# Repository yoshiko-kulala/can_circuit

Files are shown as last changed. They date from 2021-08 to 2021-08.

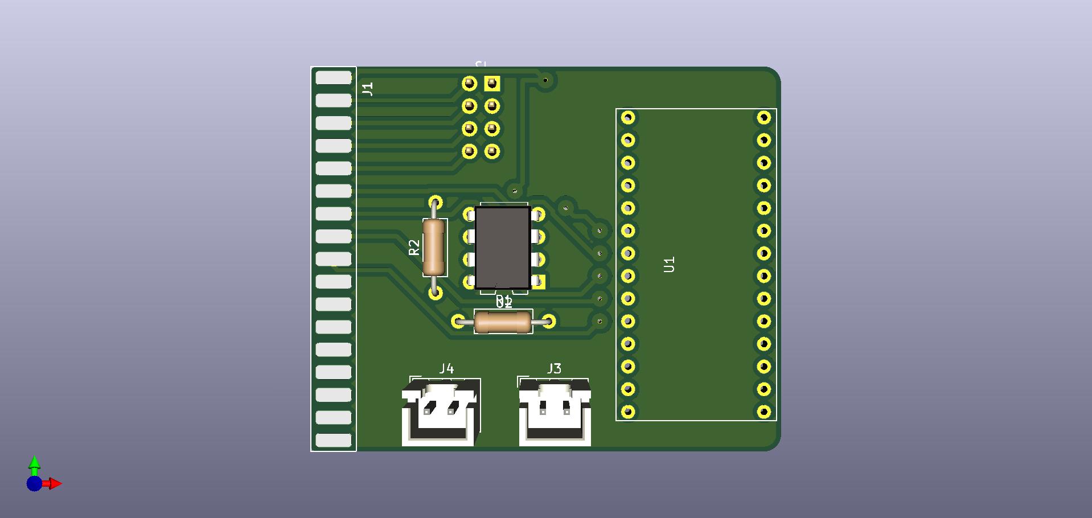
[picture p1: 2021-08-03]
RIOboard/circuit/RIOboard/RIOboard.jpg

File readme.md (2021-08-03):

# ロボット用can通信基板
このリポジトリはcan通信を用いてロボットのセンサやアクチュエータと通信・制御するための基板が置いてあります。  

各基板ごとに回路図、kicadプロジェクトデータ、サンプルプログラムが含まれます。  
自由に複製してロボットに用いることが出来ます。

can通信のid、内容については下記の各項目で示します。
通信速度は1Mbpsです。

## bumperboard
デジタルのスイッチとADCの信号を読み取ることが出来ます。  
デジタル信号が4つ、ADCは8bitが8チャネルあります。  
メインMCUにはteensy3.2を使用、can通信の通信内容は以下の通りです。  
### 0x001
| buf[1] | 中身 | 備考 |
| --- | --- | --- |
| buf[0] | デジタル信号 | 4つの入力の論理和 |
### 0x003
| buf[8] | 中身 | 備考 |
| --- | --- | --- |
| buf[0] | A0 | 0~255 |
| buf[1] | A1 |  |
| buf[2] | A2 |  |
| buf[3] | A3 |  |
| buf[4] | A4 |  |
| buf[5] | A5 |  |
| buf[6] | A6 |  |
| buf[7] | A7 |  |

## encoderboard  
インクリメントエンコーダを読み取り、回転速度と積分量を返します。  
エンコーダは最大3つまで搭載できます。
MCUにはstm32f303k8を使用し、ハードウェアデコーダを用いてエンコーダの読み取りを行っています。
can通信の内容は以下の通りです。
### 0x301
| buf[8] | 中身 | 備考 |
| --- | --- | --- |
| buf[0] | エンコーダ0のカウント下8bit | 速度は10bit |
| buf[1] | エンコーダ0のカウント上2bitとエンコーダ1のカウント下6bit |  |
| buf[2] | エンコーダ1のカウント下4bitとエンコーダ2のカウント下4bit |  |
| buf[3] | エンコーダ2のカウント下6bit |  |
| buf[4] | 未使用 |  |
| buf[5] | 未使用 |  |
| buf[6] | 未使用 |  |
| buf[7] | 未使用 |  |
### 0x302
| buf[8] | 中身 | 備考 |
| --- | --- | --- |
| buf[0] | エンコーダ0のカウント下8bit | 上下合成して0~65536 |
| buf[1] | エンコーダ0のカウント上8bit |  |
| buf[2] | エンコーダ1のカウント下8bit | 上下合成して0~65536 |
| buf[3] | エンコーダ1のカウント上8bit |  |
| buf[4] | エンコーダ2のカウント下8bit | 上下合成して0~65536 |
| buf[5] | エンコーダ2のカウント上8bit |  |
| buf[6] | 未使用 |  |
| buf[7] | 未使用 |  |

## purin_main_board  
ブザーやジャイロ、コントローラ用の通信口を持った基板  
モータドライバとも接続可能で足回りの駆動系と通信することが出来る  
DJIのDR16と接続することでコントローラとの通信も可能
この基板についてはデバッグ用のcan受信プログラムが書かれている。使途に合わせて自由な内容を受信し、それに合わせてブザーを鳴らしたりモータを動かすことが可能である。

## RIOboard  
myRIOと接続し、can通信とmyRIOをつなげる基板  
myRIOとはGPIO4つとuartで接続されている。
また、myRIOからスレーブコントローラ用へのUSBコネクタも内包している。
この基板もmyRIOからの信号に合わせて自由に通信内容を決めることが出来る。

## stepperboard  
ステッピングモータを駆動させるための基板  
L6470とSPI通信を行い、最大3つのステッピングモータを駆動可能  
電源供給用のコネクタやリミットスイッチの入力コネクタも実装済  
サーボを1つまで接続し動作させることが出来る  
can通信の内容は以下の通り  
### 0x2F1
| buf[8] | 中身 | 備考 |
| --- | --- | --- |
| buf[0] | 現在のx軸(左右)の下8bit | x上限は4374  センターは2768 |
| buf[1] | 現在のx軸(左右)の上8bit | 下限が左 |
| buf[2] | 現在のy軸(上下)の下8bit | y上限は4050 |
| buf[3] | 現在のy軸(上下)の上8bit | 下限が上 |
| buf[4] | 現在のz軸(前後)の下8bit | z上限は31500 |
| buf[5] | 現在のz軸(前後)の上8bit | 下限が後 |
| buf[6] | ハンド | 1で閉じてる、0で開いてる |
| buf[7] | 未使用 |  |
### 0x2F2
| buf[8] | 中身 | 備考 |
| --- | --- | --- |
| buf[0] | 目標のx軸(左右)の下8bit | x上限は4374  センターは2768 |
| buf[1] | 目標のx軸(左右)の上8bit | 下限が左 |
| buf[2] | 目標のy軸(上下)の下8bit | y上限は4050 |
| buf[3] | 目標のy軸(上下)の上8bit | 下限が上 |
| buf[4] | 目標のz軸(前後)の下8bit | z上限は31500 |
| buf[5] | 目標のz軸(前後)の上8bit | 下限が後 |
| buf[6] | ホーム復帰 | 1でホーム復帰 |
| buf[7] | 未使用 |  |
### 0x2F3
msg.len=1
| buf[1] | 中身 | 備考 |
| --- | --- | --- |
| buf[0] | ハンド開閉 | 0が閉じている、1が開いてる |

## UIboard  
デジタルの信号入力が4つ、ws2812bというマイコン内蔵RGBLEDの制御信号を出すことが出来る  
非常停止スイッチが取り付けられることを想定してcanのidは0となっており最優先で信号が送られる。  
通信内容は以下の通り。  
### 0x000
| buf[8] | 中身 | 備考 |
| --- | --- | --- |
| buf[0] | 状態 | 現在のライトの色 |
| buf[1] | 非常停止スイッチ | 押下状態で0 |
| buf[2] | リセットスイッチ | 押下状態で0 |
| buf[3] | 起動スイッチ | 押下状態で0 |
| buf[4] | 空き | 押下状態で0 |
| buf[5] | 未使用 |  |
| buf[6] | 未使用 |  |
| buf[7] | 未使用 |  |

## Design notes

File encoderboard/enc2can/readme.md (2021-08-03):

# enc2can

エンコーダを読んでcanで送る基板とプログラム  

送信側はnucleo f303k8  
受信側はteensy3.2

トランシーバーはmcp2551  

canidは0x301(切り替えるdipを基板につけ忘れたので...)

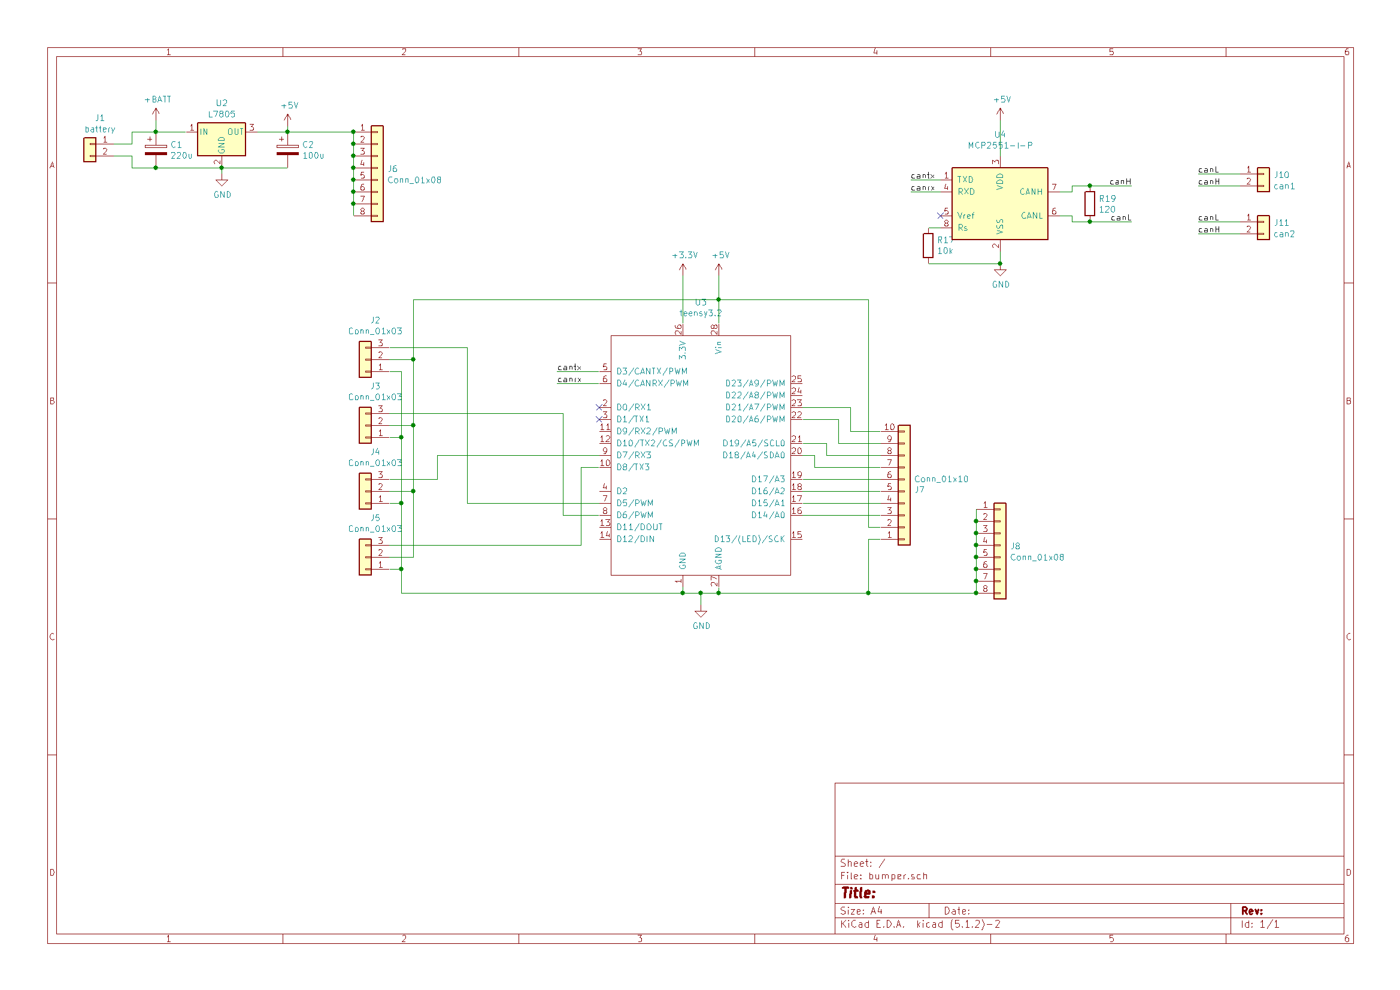
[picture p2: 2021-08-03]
bumperboard/circuit/circuit.png

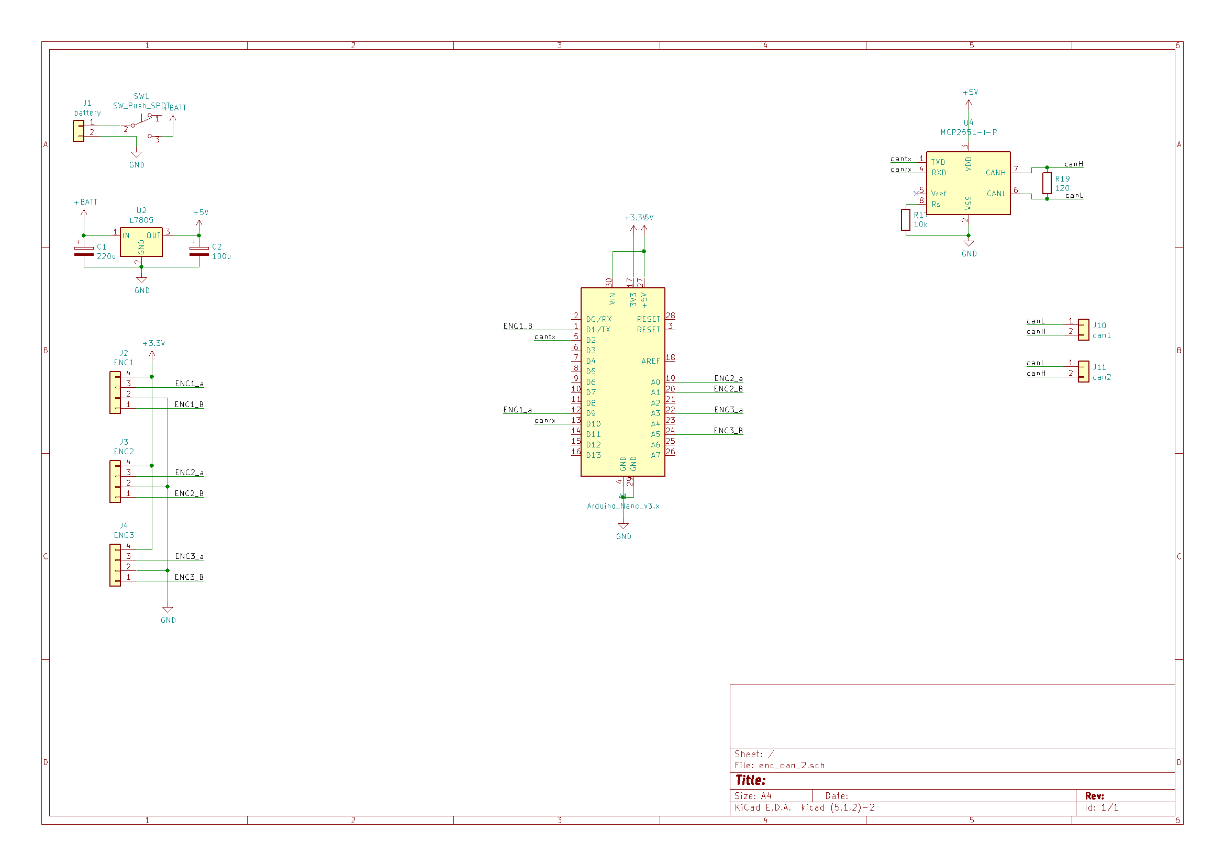
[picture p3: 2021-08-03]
encoderboard/circuit/circuit.png

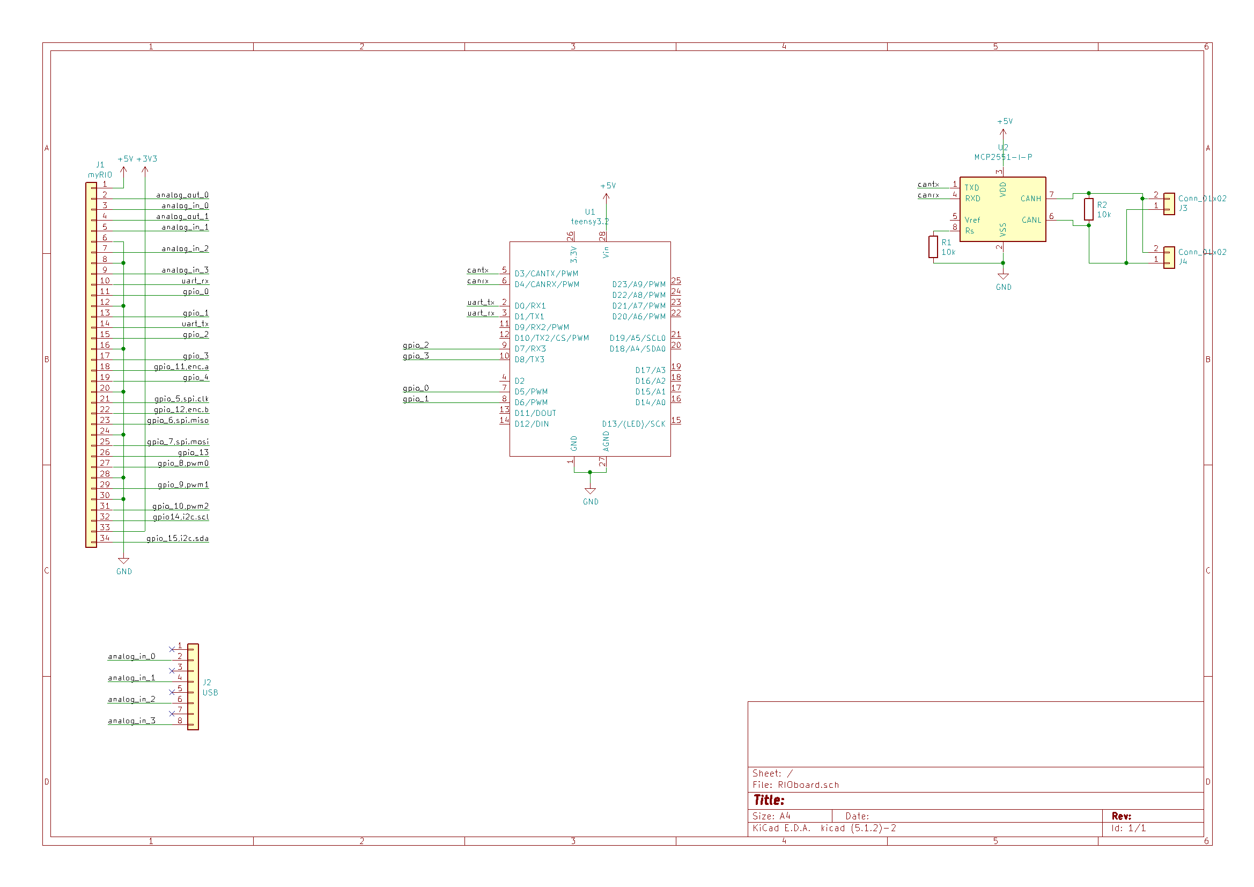
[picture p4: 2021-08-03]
RIOboard/circuit/circuit.png

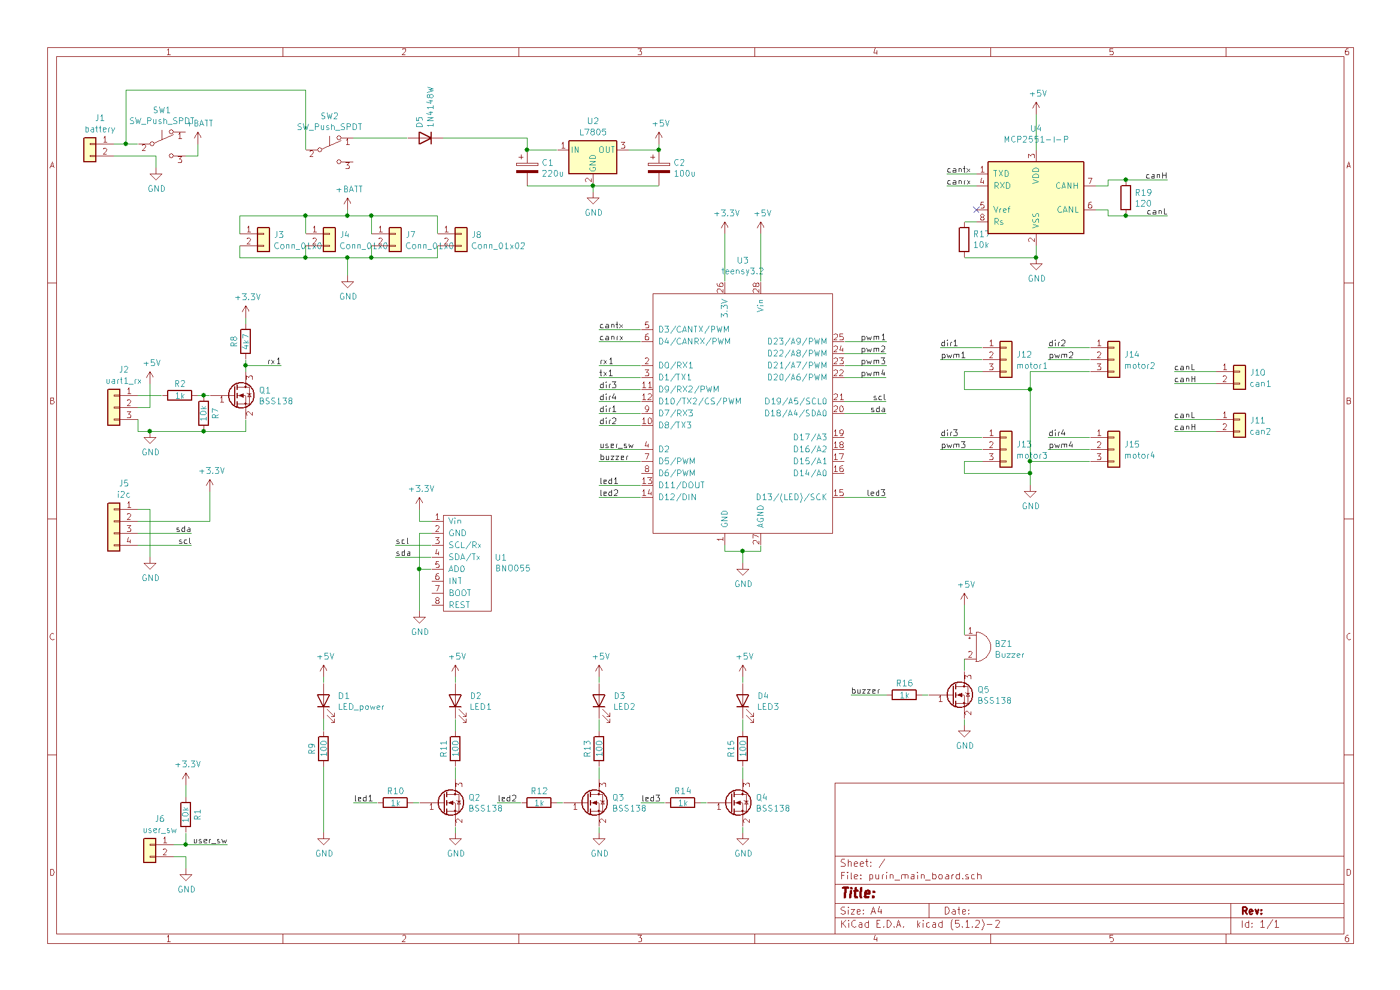
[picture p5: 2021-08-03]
purin_main_board/circuit/circuit.png

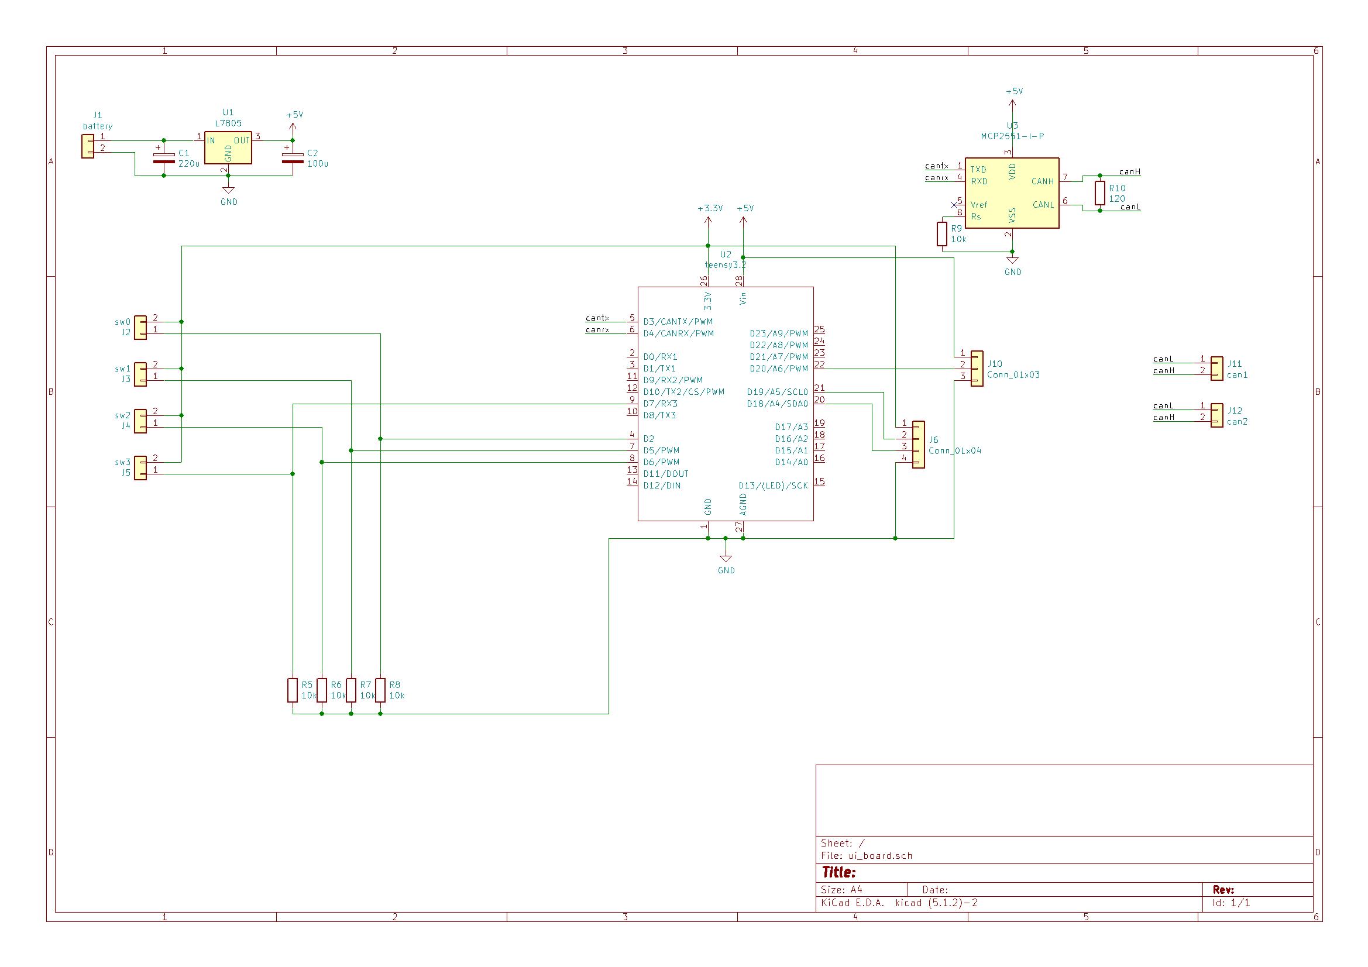
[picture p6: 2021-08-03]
UIboard/circuit/circuit.png

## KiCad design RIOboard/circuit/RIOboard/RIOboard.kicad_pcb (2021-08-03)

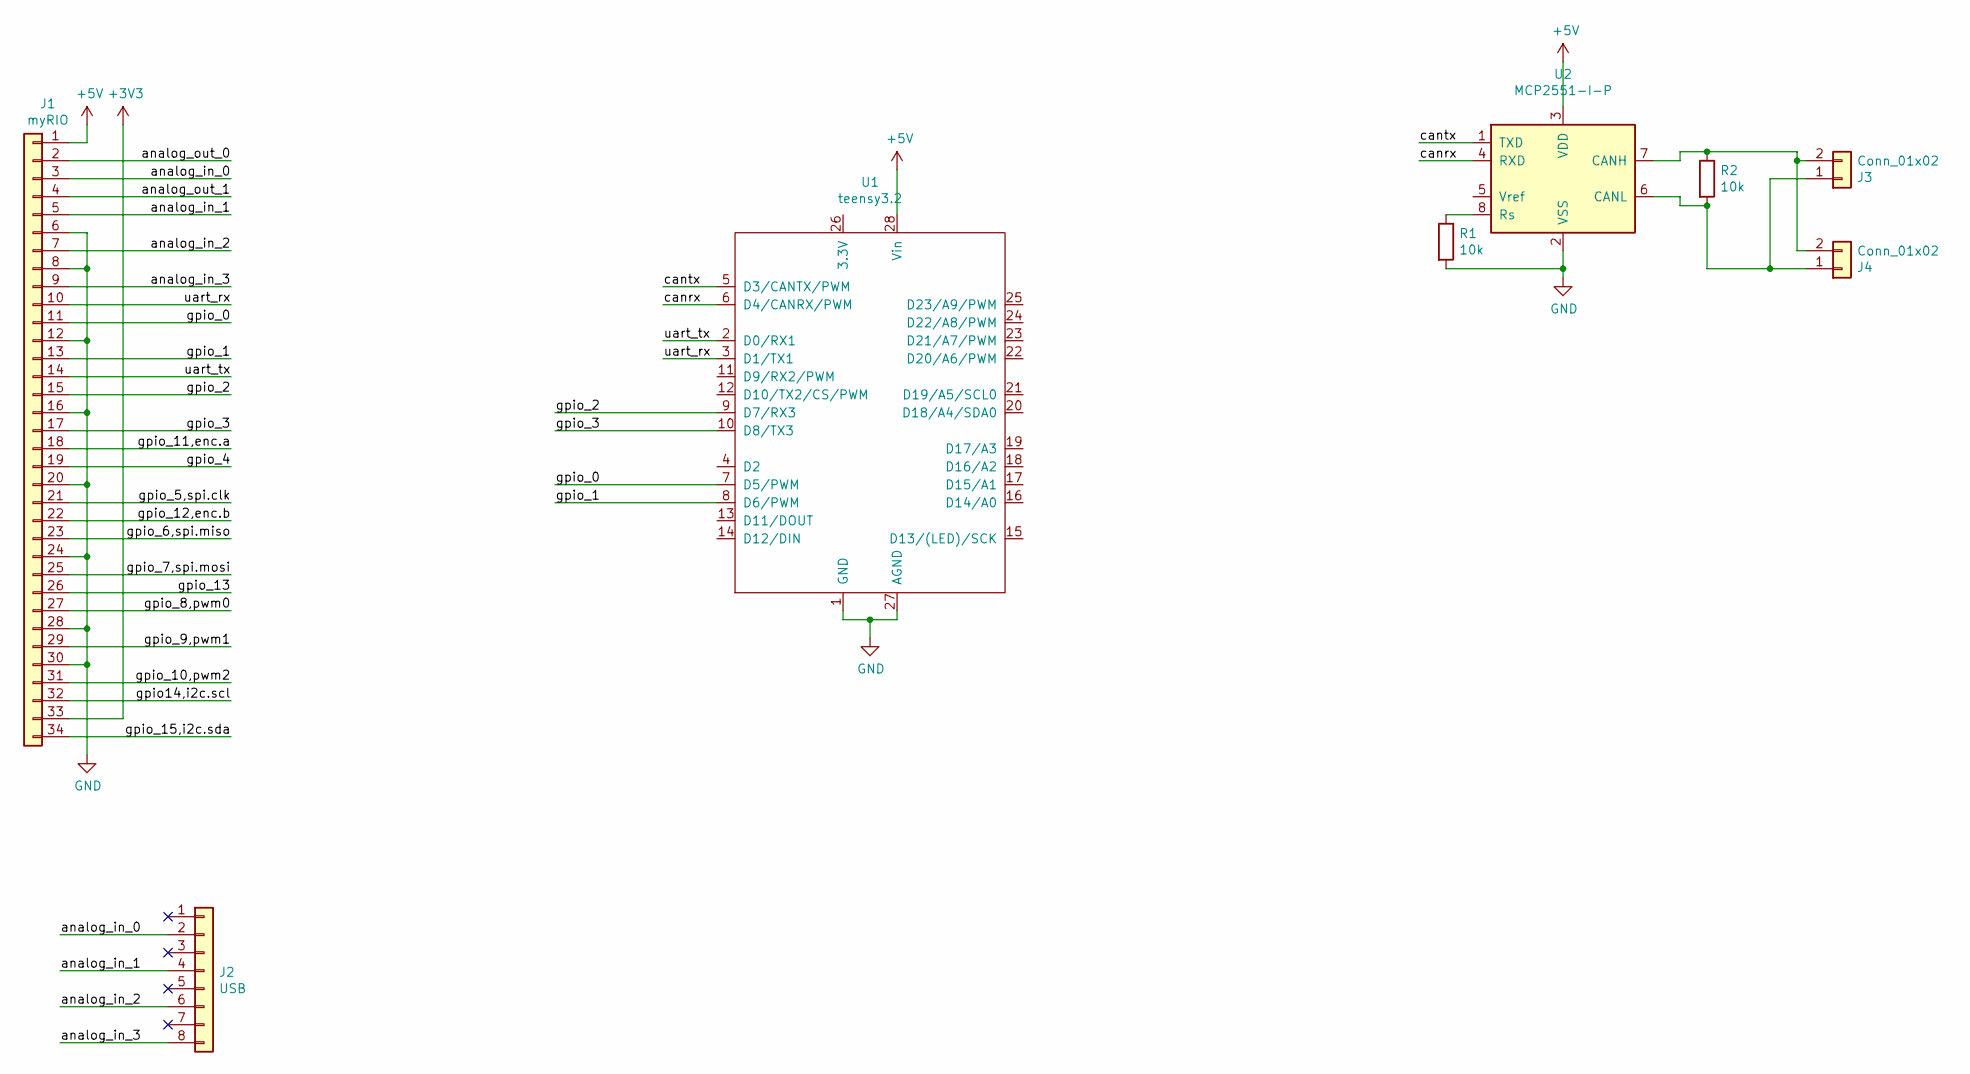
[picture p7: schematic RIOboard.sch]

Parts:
J1: myRIO; yokodasipinsoket
J2: USB; PinHeader_2x04_P2.54mm_Vertical
J3, J4: Conn_01x02; JST_XH_B2B-XH-A_1x02_P2.50mm_Vertical
R1, R2: 10k; R_Axial_DIN0207_L6.3mm_D2.5mm_P10.16mm_Horizontal
U1: teensy3.2
U2: MCP2551-I-P; DIP-8_W7.62mm

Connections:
+3V3: J1.33
+5V: J1.1, U1.28 (Vin), U2.3 (VDD); also elsewhere on the board
/analog_in_0: J1.3, J2.2
/analog_in_1: J1.5, J2.4
/analog_in_2: J1.7, J2.6
/analog_in_3: J1.9, J2.8
/analog_out_0: J1.2
/analog_out_1: J1.4
/canrx: U1.6 (D4/CANRX/PWM), U2.4 (RXD)
/cantx: U1.5 (D3/CANTX/PWM), U2.1 (TXD)
/gpio14,i2c.scl: J1.32
/gpio_0: J1.11, U1.7 (D5/PWM)
/gpio_1: J1.13, U1.8 (D6/PWM)
/gpio_2: J1.15, U1.9 (D7/RX3)
/gpio_3: J1.17, U1.10 (D8/TX3)
/gpio_4: J1.19
/gpio_5,spi.clk: J1.21
/gpio_6,spi.miso: J1.23
/gpio_7,spi.mosi: J1.25
/gpio_8,pwm0: J1.27
/gpio_9,pwm1: J1.29
/gpio_10,pwm2: J1.31
/gpio_11,enc.a: J1.18
/gpio_12,enc.b: J1.22
/gpio_13: J1.26
/gpio_15,i2c.sda: J1.34
/uart_rx: J1.10, U1.3 (D1/TX1)
/uart_tx: J1.14, U1.2 (D0/RX1)
GND: J1.6, J1.8, J1.12, J1.16, J1.20, J1.24, J1.28, J1.30, R1.2, U1.1 (GND), U1.27 (AGND), U2.2 (VSS); also elsewhere on the board
unnamed 29: U1.11 (D9/RX2/PWM); also elsewhere on the board
unnamed 30: U1.12 (D10/TX2/CS/PWM); also elsewhere on the board
unnamed 32: U1.19 (D17/A3); also elsewhere on the board
unnamed 33: U1.18 (D16/A2); also elsewhere on the board
unnamed 34: U1.17 (D15/A1); also elsewhere on the board
unnamed 35: U1.16 (D14/A0); also elsewhere on the board
unnamed: J3.1, J4.1, R2.2, U2.6 (CANL)
unnamed: J3.2, J4.2, R2.1, U2.7 (CANH)
unnamed: R1.1, U2.8 (Rs)

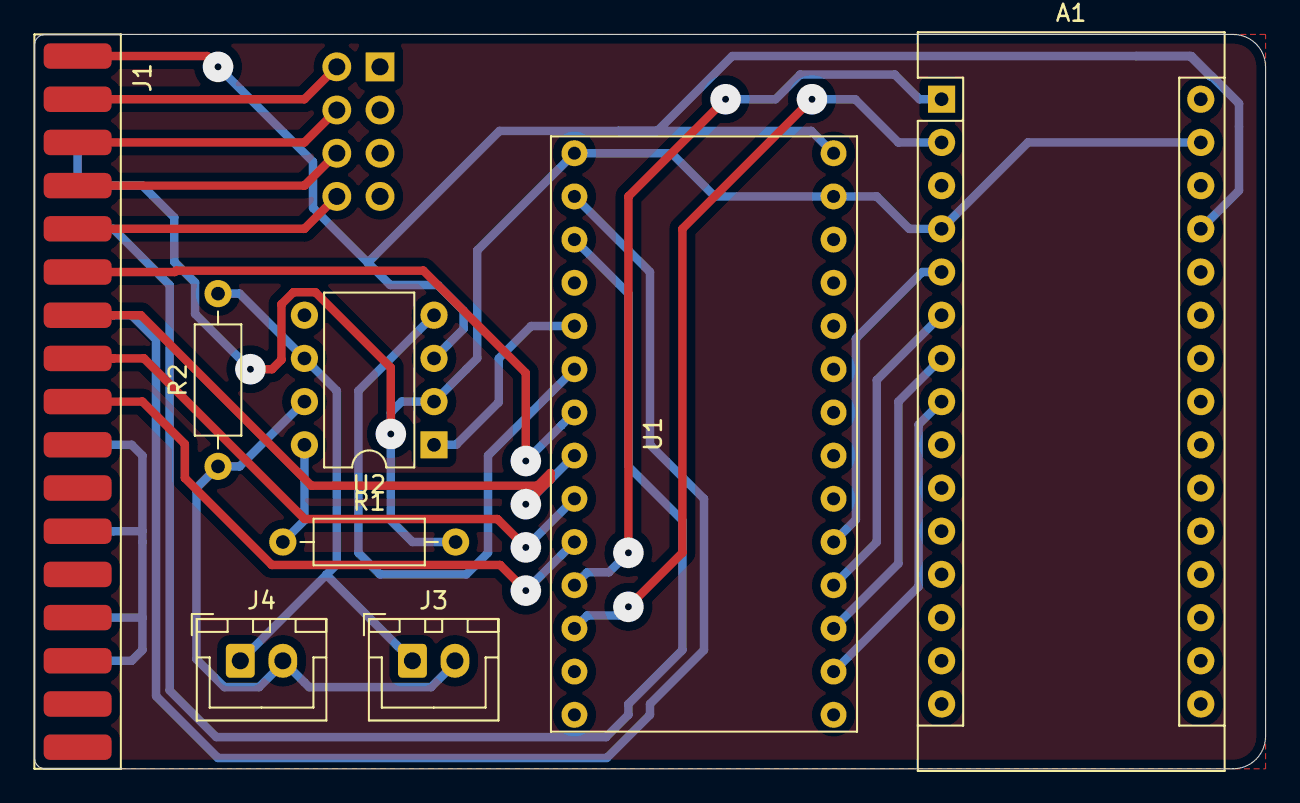
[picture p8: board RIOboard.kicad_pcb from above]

Board: 2 copper layers, 72.4 x 43.2 mm, 9 parts (1 on the bottom side), 23 nets.

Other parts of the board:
A1: Arduino_Nano_v3.x; Arduino_Nano

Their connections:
+5V: A1.27; also elsewhere on the board
GND: A1.4, A1.29; also elsewhere on the board
unnamed 29: A1.1; also elsewhere on the board
unnamed 30: A1.2; also elsewhere on the board
unnamed 32: A1.5; also elsewhere on the board
unnamed 33: A1.6; also elsewhere on the board
unnamed 34: A1.7; also elsewhere on the board
unnamed 35: A1.8; also elsewhere on the board

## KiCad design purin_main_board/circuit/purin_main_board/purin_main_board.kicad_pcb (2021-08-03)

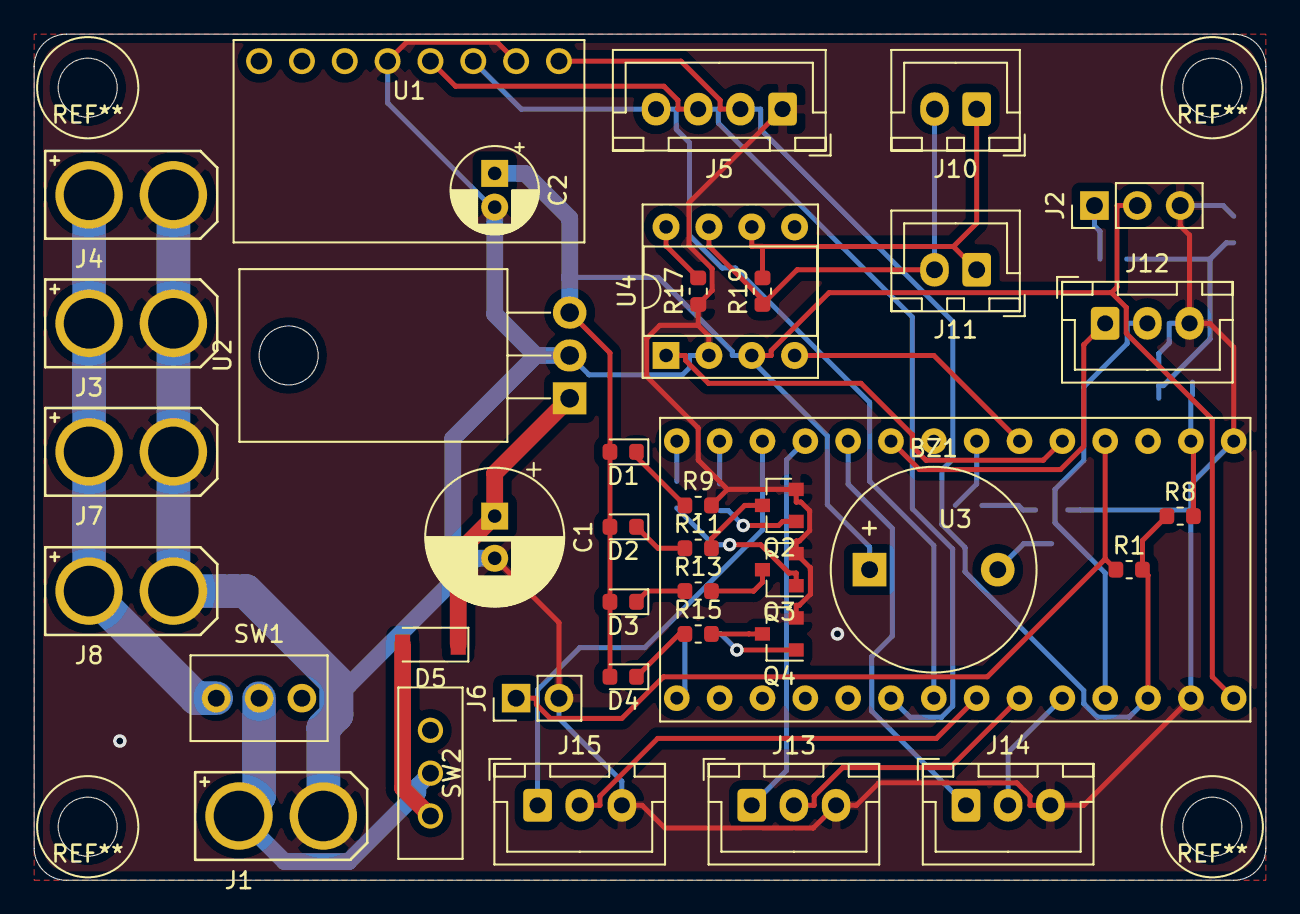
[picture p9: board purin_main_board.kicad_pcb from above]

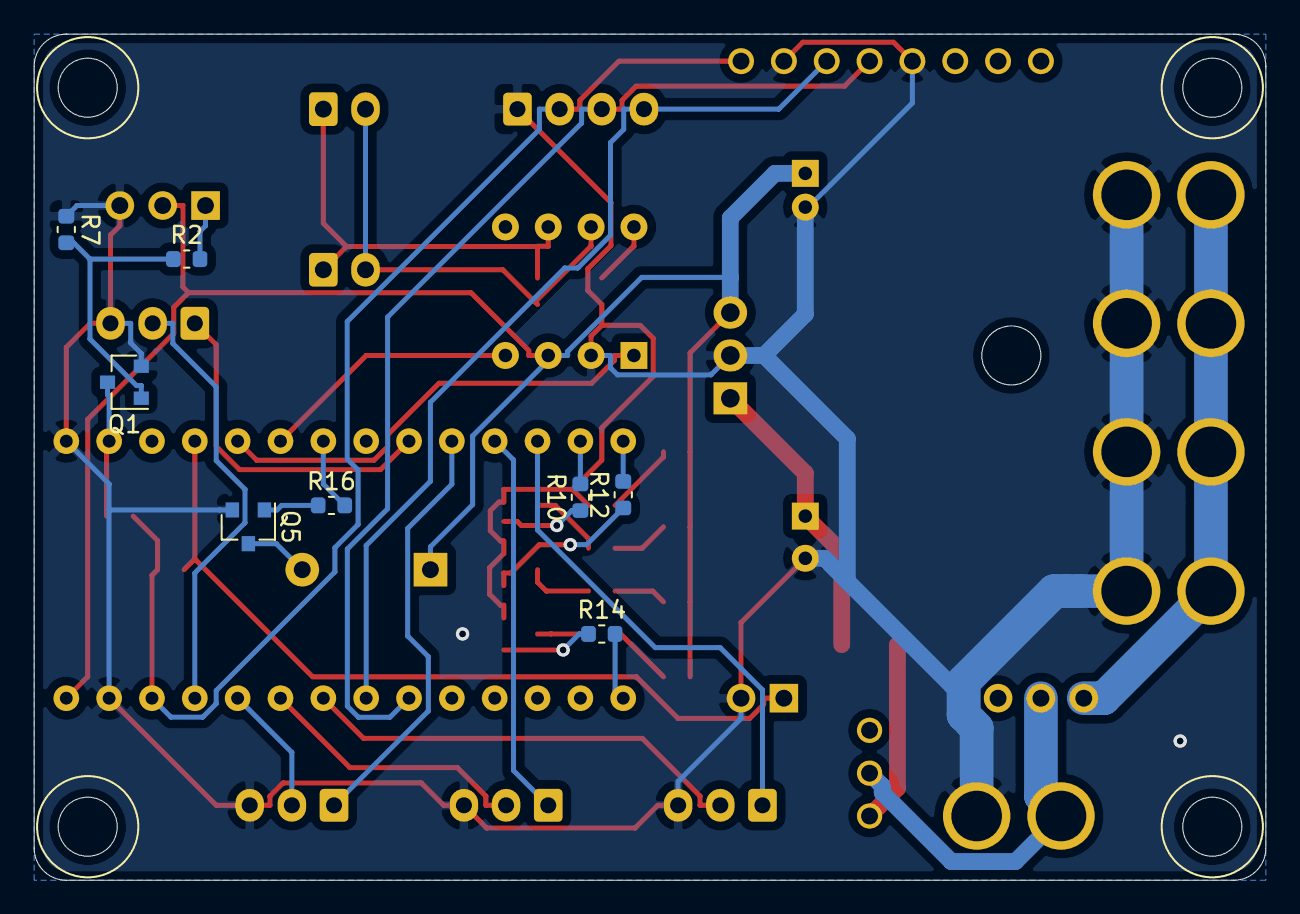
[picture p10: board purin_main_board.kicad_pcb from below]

Board: 2 copper layers, 73.0 x 50.2 mm, 47 parts (8 on the bottom side), 42 nets.

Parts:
BZ1: Buzzer; Buzzer_12x9.5RM7.6
C1: 220u; CP_Radial_D8.0mm_P2.50mm
C2: 100u; CP_Radial_D5.0mm_P2.00mm
D1: LED_power; LED_0603_1608Metric
D2: LED1; LED_0603_1608Metric
D3: LED2; LED_0603_1608Metric
D4: LED3; LED_0603_1608Metric
D5: 1N4148W; D_SOD-123
J1: battery; xt30u-f
J2: uart1_rx; PinHeader_1x03_P2.54mm_Vertical
J3, J4, J7, J8: Conn_01x02; xt30u-f
J5: i2c; JST_XH_B4B-XH-A_1x04_P2.50mm_Vertical
J6: user_sw; PinHeader_1x02_P2.54mm_Vertical
J10: can1; JST_XH_B2B-XH-A_1x02_P2.50mm_Vertical
J11: can2; JST_XH_B2B-XH-A_1x02_P2.50mm_Vertical
J12: motor1; JST_XH_B3B-XH-A_1x03_P2.50mm_Vertical
J13: motor3; JST_XH_B3B-XH-A_1x03_P2.50mm_Vertical
J14: motor2; JST_XH_B3B-XH-A_1x03_P2.50mm_Vertical
J15: motor4; JST_XH_B3B-XH-A_1x03_P2.50mm_Vertical
Q1, Q2, Q3, Q4, Q5: BSS138; SOT-23
R1, R7, R17: 10k; R_0603_1608Metric
R2, R10, R12, R14, R16: 1k; R_0603_1608Metric
R8: 4k7; R_0603_1608Metric
R9, R11, R13, R15: 100; R_0603_1608Metric
R19: 120; R_0603_1608Metric
SW1: SW_Push_SPDT; toggle
SW2: SW_Push_SPDT; mini_sw
U1: BNO055
U2: L7805; TO-220-3_Horizontal_TabDown
U3: teensy3.2
U4: MCP2551-I-P; DIP-8_W7.62mm_Socket

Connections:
+3V3: J5.2, R1.2, R8.1, U1.1, U3.26
+5V: BZ1.1, C2.1, D1.2, D2.2, D3.2, D4.2, J2.2, U2.3, U3.28, U4.3
+BATT: J3.1, J4.1, J7.1, J8.1, SW1.3
/buzzer: R16.2, U3.7
/canH: J10.2, J11.2, R19.1, U4.7
/canL: J10.1, J11.1, R19.2, U4.6
/canrx: U3.6, U4.4
/cantx: U3.5, U4.1
/dir1: J12.1, U3.9
/dir2: J14.1, U3.10
/dir3: J13.1, U3.11
/dir4: J15.1, U3.12
/led1: R10.2, U3.13
/led2: R12.2, U3.14
/led3: R14.2, U3.15
/pwm1: J12.2, U3.25
/pwm2: J14.2, U3.24
/pwm3: J13.2, U3.23
/pwm4: J15.2, U3.22
/rx1: Q1.3, R8.2, U3.2
/scl: J5.4, U1.3, U3.21
/sda: J5.3, U1.4, U3.20
/user_sw: J6.1, R1.1, U3.4
GND: C1.2, C2.2, J1.2, J2.3, J3.2, J4.2, J5.1, J6.2, J7.2, J8.2, J12.3, J13.3, J14.3, J15.3, Q1.2, Q2.2, Q3.2, Q4.2, Q5.2, R7.1, R9.2, R17.1, U1.2, U1.5, U2.2, U3.1, U3.27, U4.2
unnamed: BZ1.2, Q5.3
unnamed: C1.1, D5.1, U2.1
unnamed: D1.1, R9.1
unnamed: D2.1, R11.1
unnamed: D3.1, R13.1
unnamed: D4.1, R15.1
unnamed: D5.2, SW2.1
unnamed: J1.1, SW1.2, SW2.2
unnamed: J2.1, R2.2
unnamed: Q1.1, R2.1, R7.2
unnamed: Q2.1, R10.1
unnamed: Q2.3, R11.2
unnamed: Q3.1, R12.1
unnamed: Q3.3, R13.2
unnamed: Q4.1, R14.1
unnamed: Q4.3, R15.2
unnamed: Q5.1, R16.1
unnamed: R17.2, U4.8

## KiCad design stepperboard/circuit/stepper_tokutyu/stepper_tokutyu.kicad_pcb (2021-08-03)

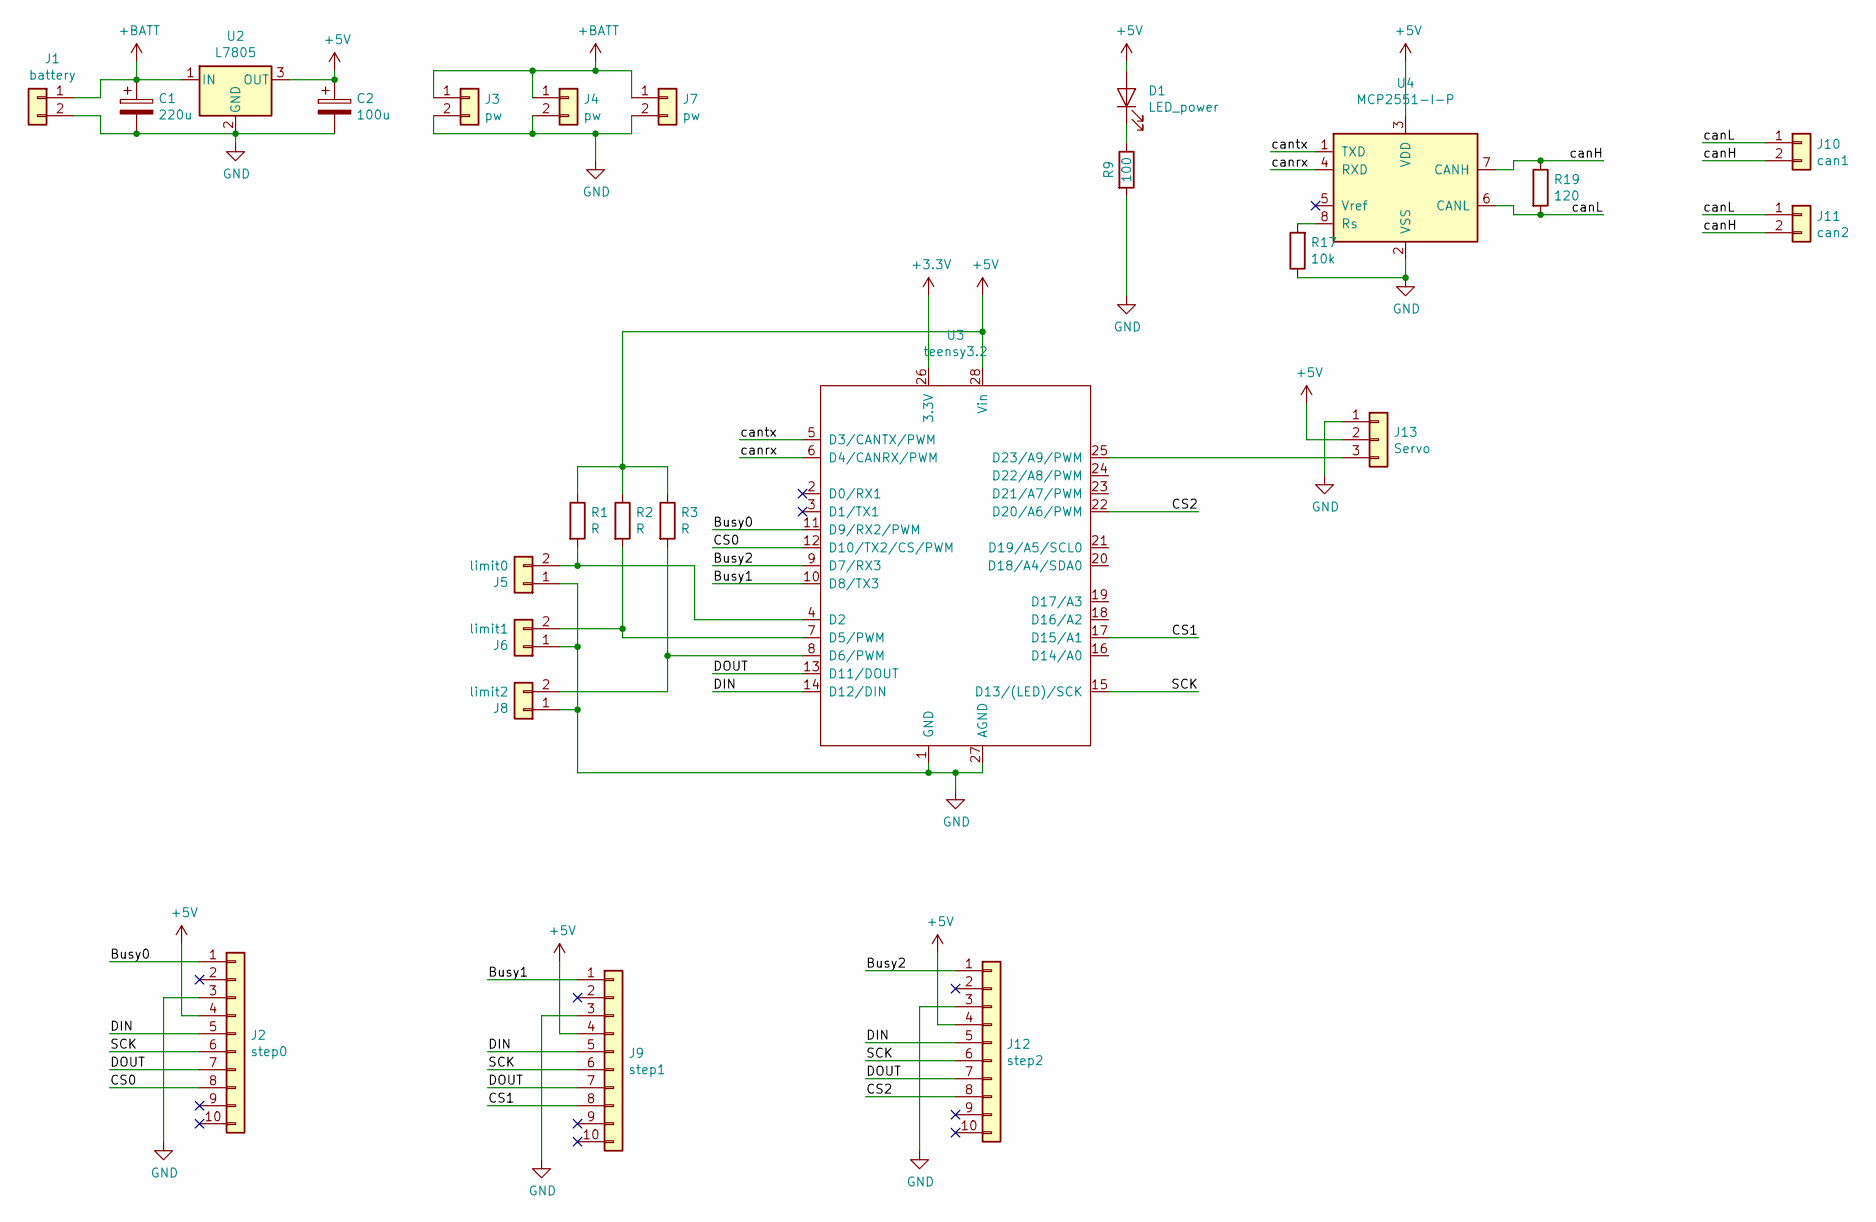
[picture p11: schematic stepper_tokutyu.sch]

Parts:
C1: 220u; CP_Radial_D8.0mm_P2.50mm
C2: 100u; CP_Radial_D5.0mm_P2.00mm
D1: LED_power; LED_D5.0mm
J1: battery; JST_XH_B2B-XH-A_1x02_P2.50mm_Vertical
J2: step0; IDC-Header_2x05_P2.54mm_Vertical
J3, J4, J7: pw; JST_XH_B2B-XH-A_1x02_P2.50mm_Vertical
J5: limit0; JST_XH_B2B-XH-A_1x02_P2.50mm_Vertical
J6: limit1; JST_XH_B2B-XH-A_1x02_P2.50mm_Vertical
J8: limit2; JST_XH_B2B-XH-A_1x02_P2.50mm_Vertical
J9: step1; IDC-Header_2x05_P2.54mm_Vertical
J10: can1; JST_XH_B2B-XH-A_1x02_P2.50mm_Vertical
J11: can2; JST_XH_B2B-XH-A_1x02_P2.50mm_Vertical
J12: step2; IDC-Header_2x05_P2.54mm_Vertical
J13: Servo; JST_XH_B3B-XH-A_1x03_P2.50mm_Vertical
R1, R2, R3: R; R_0603_1608Metric
R9: 100; R_0603_1608Metric
R17: 10k; R_0603_1608Metric
R19: 120; R_0603_1608Metric
U2: L7805; TO-220-3_Vertical
U3: teensy3.2
U4: MCP2551-I-P; DIP-8_W7.62mm_Socket

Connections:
+3V3: U3.26 (3.3V)
+5V: C2.1, D1.2 (A), J2.4, J9.4, J12.4, J13.2, R1.1, R2.1, R3.1, U2.3 (OUT), U3.28 (Vin), U4.3 (VDD)
+BATT: C1.1, J1.1, J3.1, J4.1, J7.1, U2.1 (IN)
/Busy0: J2.1, U3.11 (D9/RX2/PWM)
/Busy1: J9.1, U3.10 (D8/TX3)
/Busy2: J12.1, U3.9 (D7/RX3)
/CS0: J2.8, U3.12 (D10/TX2/CS/PWM)
/CS1: J9.8, U3.17 (D15/A1)
/CS2: J12.8, U3.22 (D20/A6/PWM)
/DIN: J2.5, J9.5, J12.5, U3.14 (D12/DIN)
/DOUT: J2.7, J9.7, J12.7, U3.13 (D11/DOUT)
/SCK: J2.6, J9.6, J12.6, U3.15 (D13/(LED)/SCK)
/canH: J10.2, J11.2, R19.1, U4.7 (CANH)
/canL: J10.1, J11.1, R19.2, U4.6 (CANL)
/canrx: U3.6 (D4/CANRX/PWM), U4.4 (RXD)
/cantx: U3.5 (D3/CANTX/PWM), U4.1 (TXD)
GND: C1.2, C2.2, J1.2, J2.3, J3.2, J4.2, J5.1, J6.1, J7.2, J8.1, J9.3, J12.3, J13.1, R9.2, R17.1, U2.2 (GND), U3.1 (GND), U3.27 (AGND), U4.2 (VSS)
unnamed: D1.1 (K), R9.1
unnamed: J5.2, R1.2, U3.4 (D2)
unnamed: J6.2, R2.2, U3.7 (D5/PWM)
unnamed: J8.2, R3.2, U3.8 (D6/PWM)
unnamed: J13.3, U3.25 (D23/A9/PWM)
unnamed: R17.2, U4.8 (Rs)

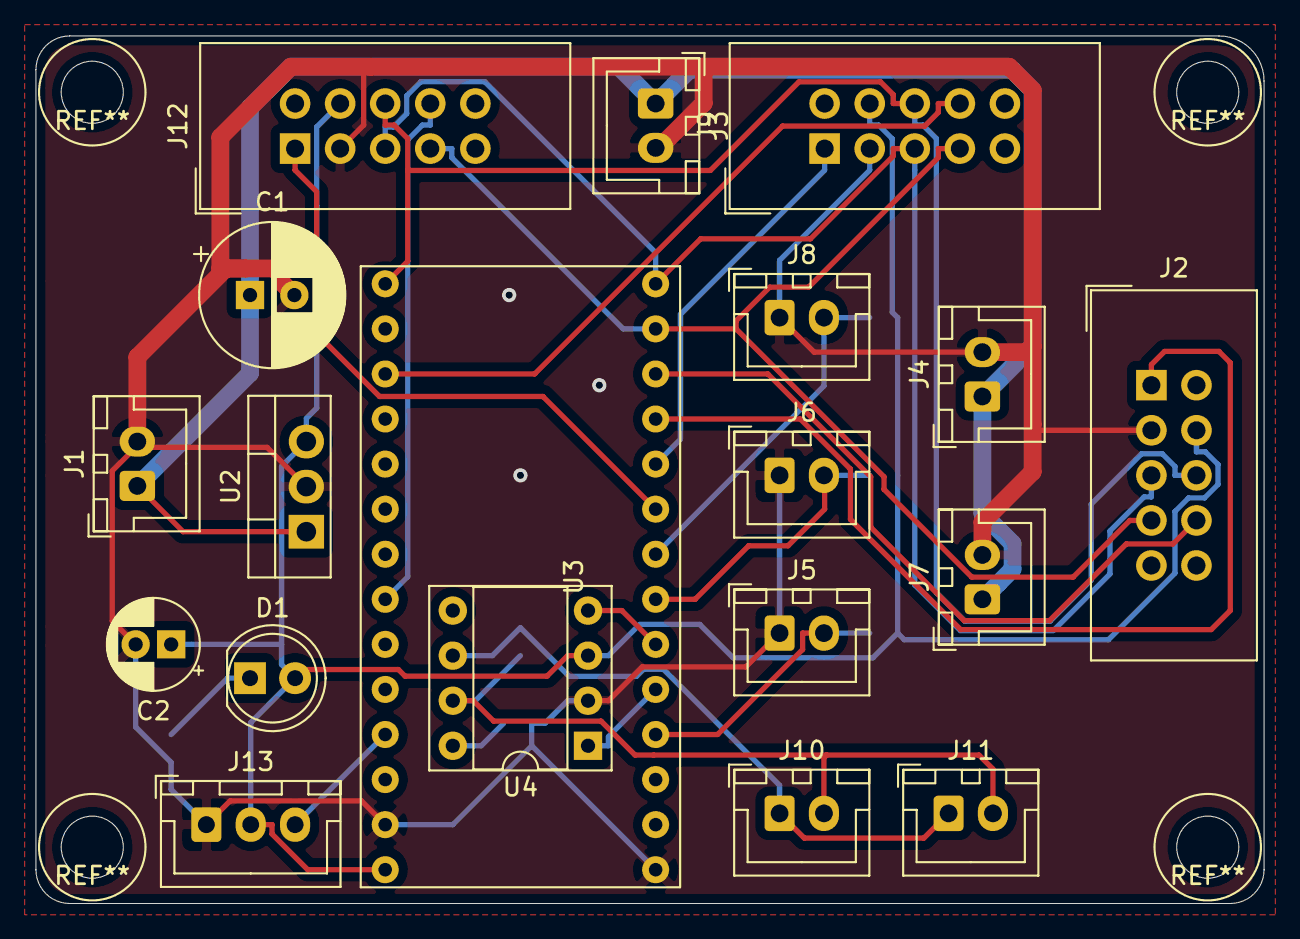
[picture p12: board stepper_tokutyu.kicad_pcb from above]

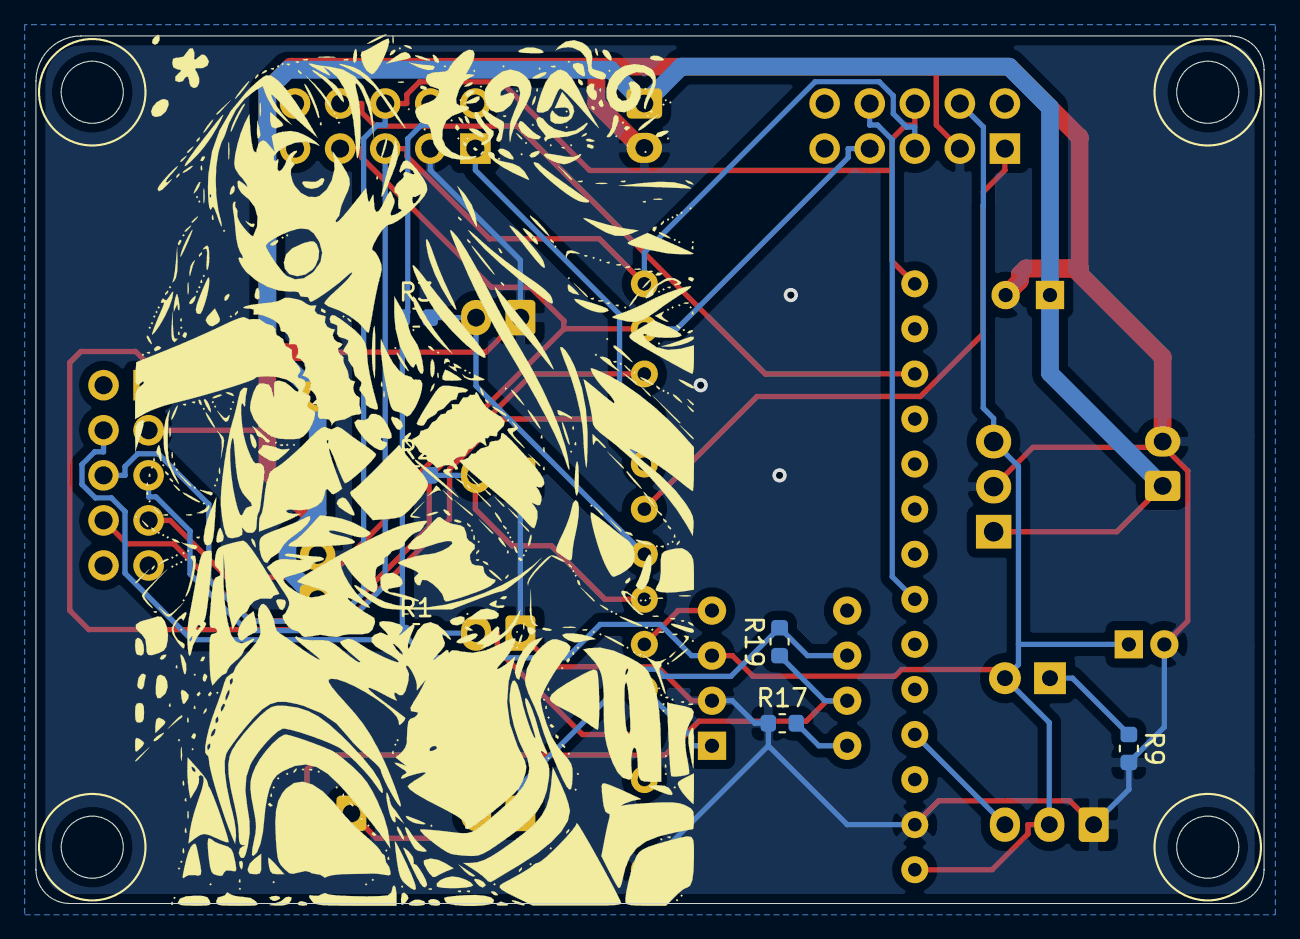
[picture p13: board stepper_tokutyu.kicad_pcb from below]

Board: 2 copper layers, 69.2 x 48.9 mm, 25 parts (6 on the bottom side), 22 nets.

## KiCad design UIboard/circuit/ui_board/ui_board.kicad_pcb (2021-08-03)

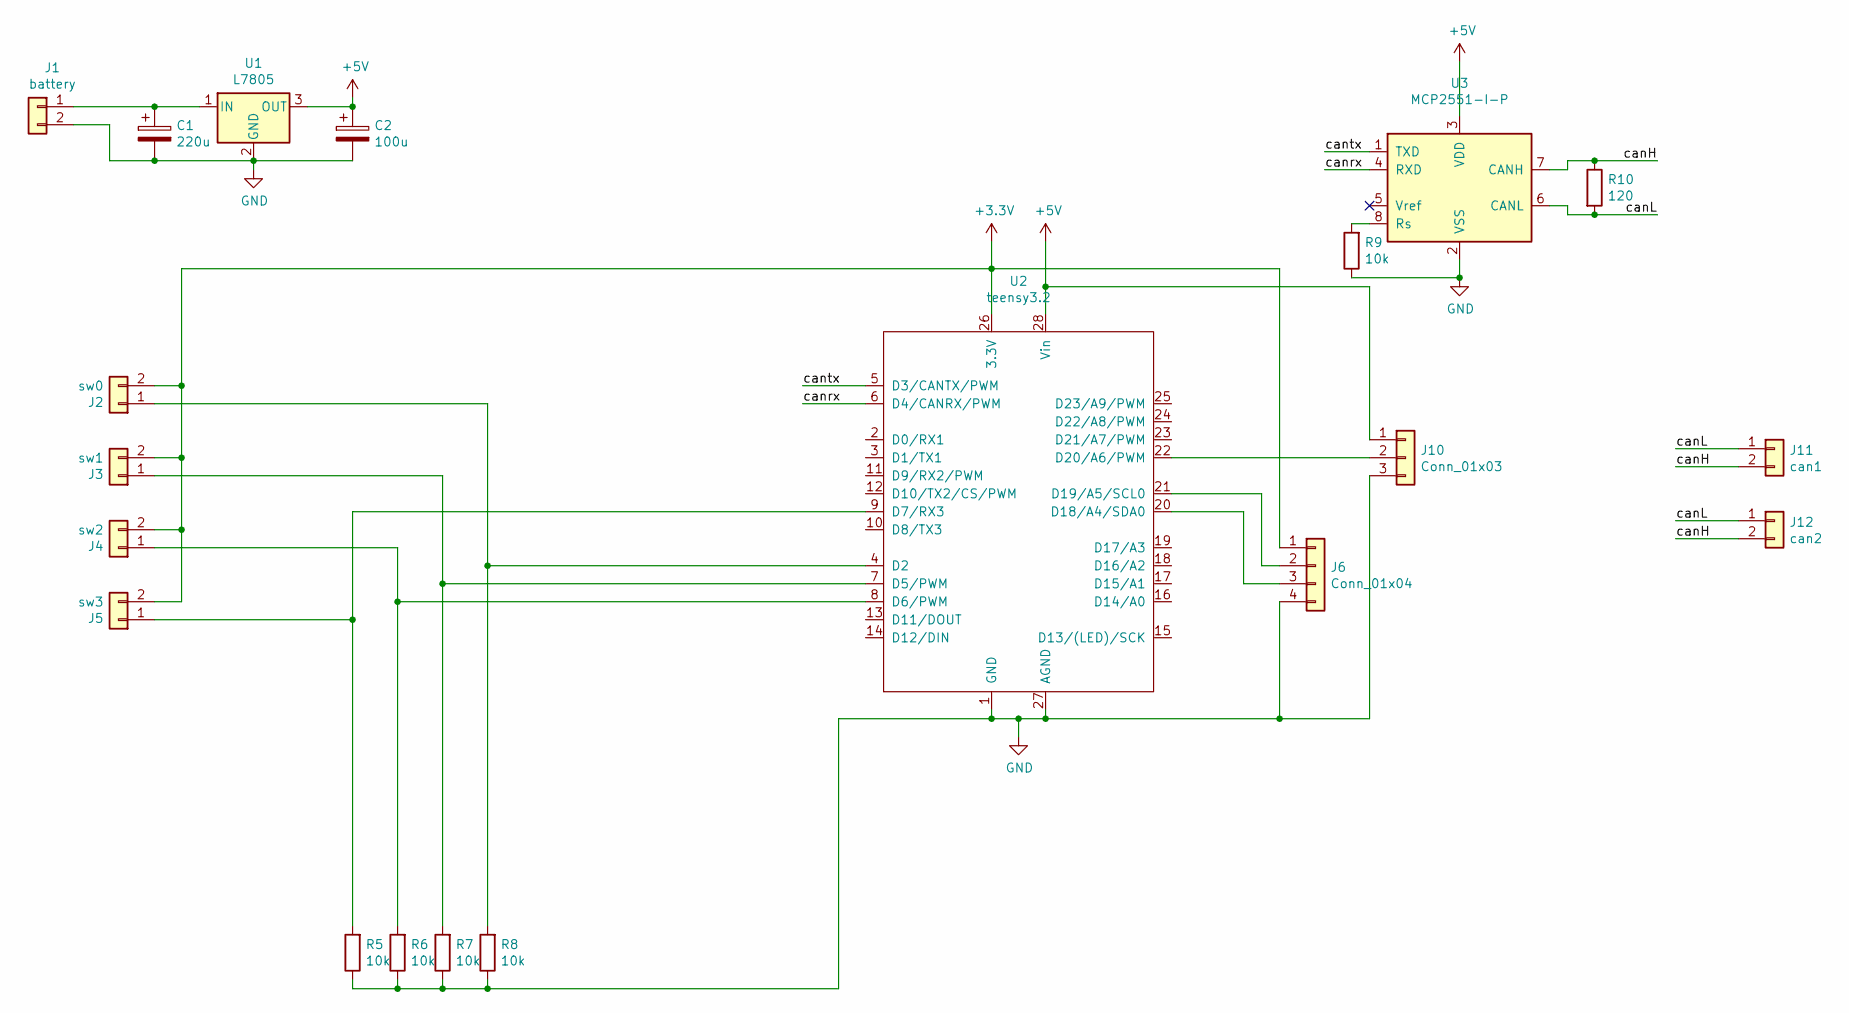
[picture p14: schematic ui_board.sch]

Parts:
C1: 220u; CP_Radial_D8.0mm_P2.50mm
C2: 100u; CP_Radial_D5.0mm_P2.00mm
J1: battery; JST_XH_B2B-XH-A_1x02_P2.50mm_Vertical
J2: sw0; JST_XH_B2B-XH-A_1x02_P2.50mm_Vertical
J3: sw1; JST_XH_B2B-XH-A_1x02_P2.50mm_Vertical
J4: sw2; JST_XH_B2B-XH-A_1x02_P2.50mm_Vertical
J5: sw3; JST_XH_B2B-XH-A_1x02_P2.50mm_Vertical
J6: Conn_01x04; JST_XH_B4B-XH-A_1x04_P2.50mm_Vertical
J10: Conn_01x03; JST_XH_B3B-XH-A_1x03_P2.50mm_Vertical
J11: can1; JST_XH_B2B-XH-A_1x02_P2.50mm_Vertical
J12: can2; JST_XH_B2B-XH-A_1x02_P2.50mm_Vertical
R5, R6, R7, R8, R9: 10k; R_Axial_DIN0207_L6.3mm_D2.5mm_P10.16mm_Horizontal
R10: 120; R_Axial_DIN0207_L6.3mm_D2.5mm_P10.16mm_Horizontal
U1: L7805; TO-220-3_Vertical
U2: teensy3.2
U3: MCP2551-I-P; DIP-8_W7.62mm_Socket

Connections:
+3V3: J2.2, J3.2, J4.2, J5.2, J6.1, U2.26 (3.3V)
+5V: C2.1, J10.1, U1.3 (OUT), U2.28 (Vin), U3.3 (VDD)
/canH: J11.2, J12.2, R10.1, U3.7 (CANH)
/canL: J11.1, J12.1, R10.2, U3.6 (CANL)
/canrx: U2.6 (D4/CANRX/PWM), U3.4 (RXD)
/cantx: U2.5 (D3/CANTX/PWM), U3.1 (TXD)
GND: C1.2, C2.2, J1.2, J6.4, J10.3, R5.1, R6.1, R7.1, R8.1, R9.1, U1.2 (GND), U2.1 (GND), U2.27 (AGND), U3.2 (VSS)
unnamed: C1.1, J1.1, U1.1 (IN)
unnamed: J2.1, R8.2, U2.4 (D2)
unnamed: J3.1, R7.2, U2.7 (D5/PWM)
unnamed: J4.1, R6.2, U2.8 (D6/PWM)
unnamed: J5.1, R5.2, U2.9 (D7/RX3)
unnamed: J6.2, U2.21 (D19/A5/SCL0)
unnamed: J6.3, U2.20 (D18/A4/SDA0)
unnamed: J10.2, U2.22 (D20/A6/PWM)
unnamed: R9.2, U3.8 (Rs)

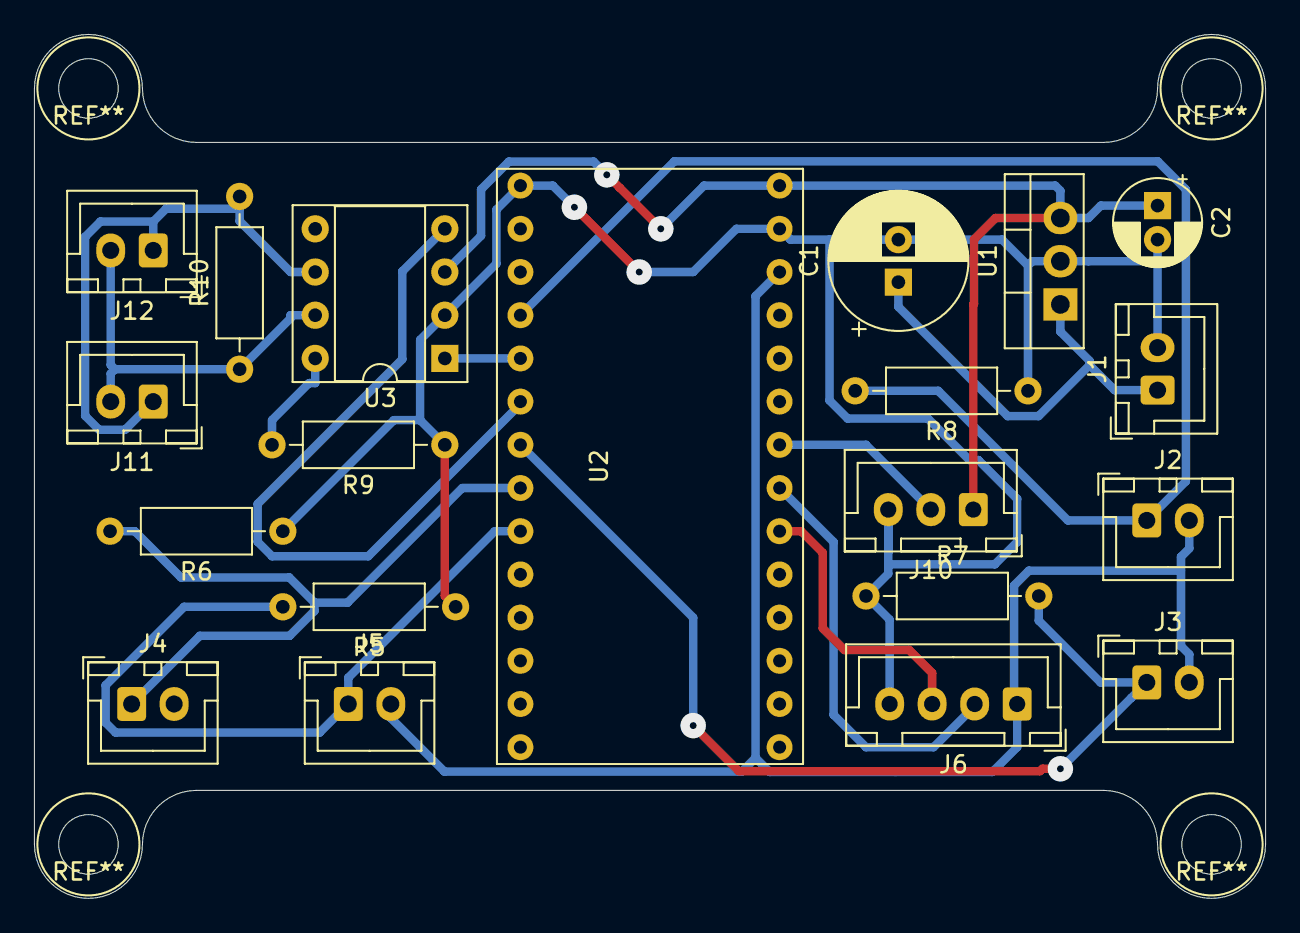
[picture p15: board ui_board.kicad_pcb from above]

Board: 2 copper layers, 72.4 x 50.8 mm, 20 parts (0 on the bottom side), 16 nets.

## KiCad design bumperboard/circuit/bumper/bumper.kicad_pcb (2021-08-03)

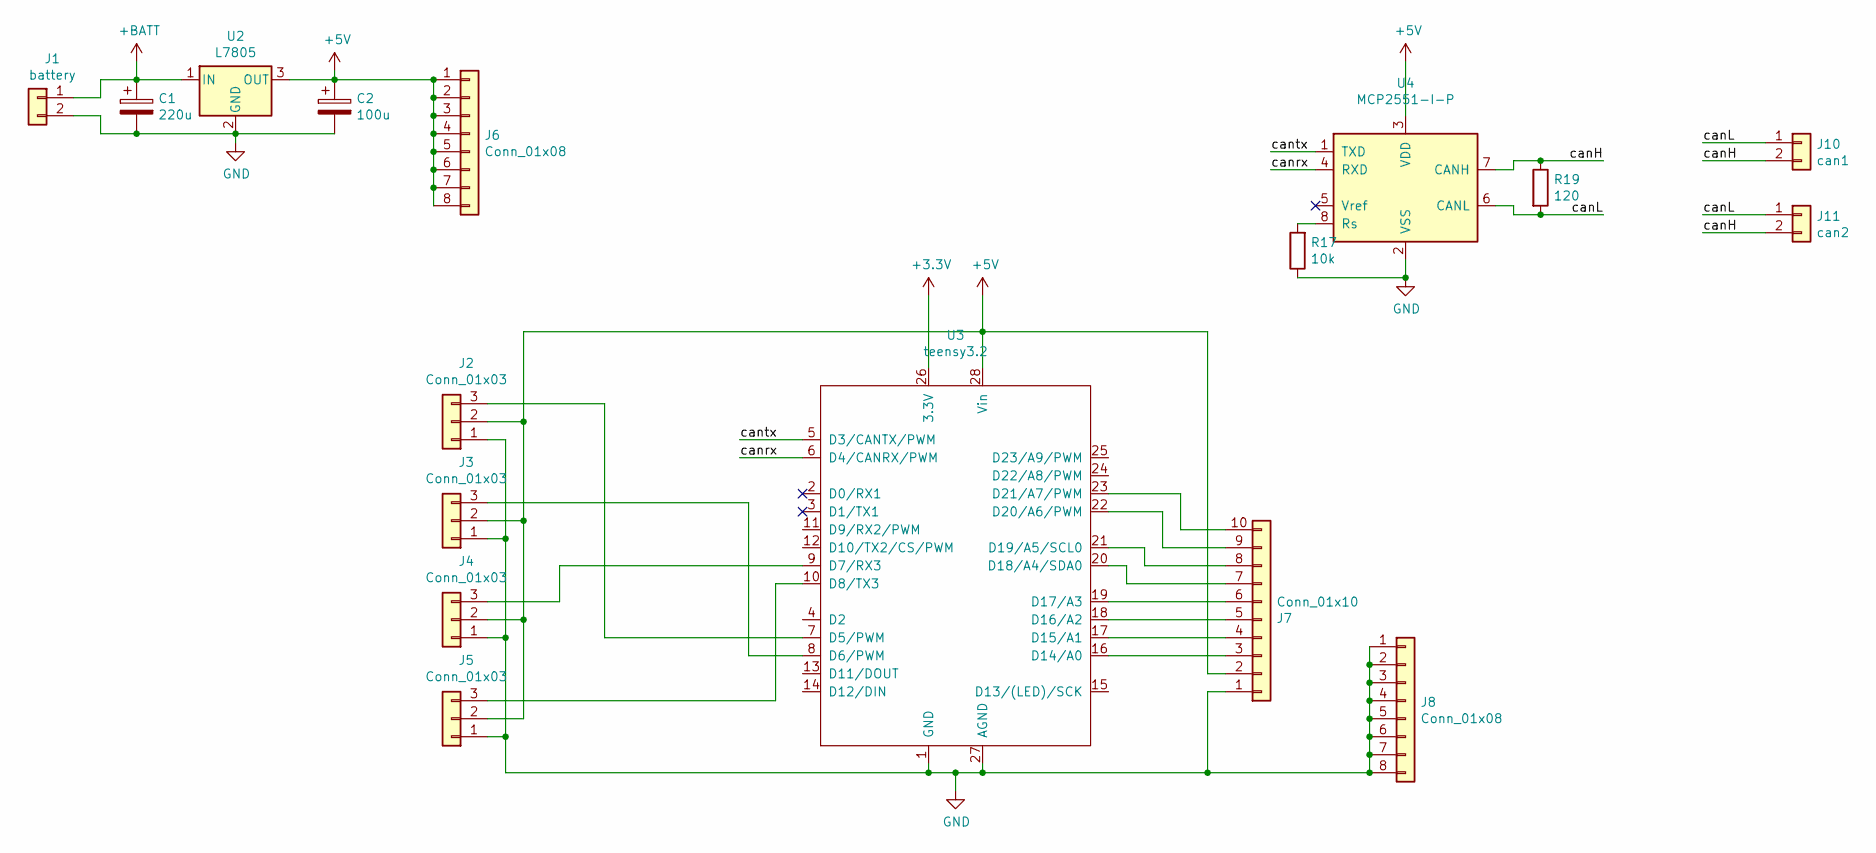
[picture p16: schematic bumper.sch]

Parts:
C1: 220u; CP_Radial_D8.0mm_P2.50mm
C2: 100u; CP_Radial_D5.0mm_P2.00mm
J1: battery; JST_XH_B2B-XH-A_1x02_P2.50mm_Vertical
J2, J3, J4, J5: Conn_01x03; JST_XH_B3B-XH-A_1x03_P2.50mm_Vertical
J6, J8: Conn_01x08; PinHeader_1x08_P2.54mm_Vertical
J7: Conn_01x10; PinHeader_1x10_P2.54mm_Vertical
J10: can1; JST_XH_B2B-XH-A_1x02_P2.50mm_Vertical
J11: can2; JST_XH_B2B-XH-A_1x02_P2.50mm_Vertical
R17: 10k; R_Axial_DIN0207_L6.3mm_D2.5mm_P10.16mm_Horizontal
R19: 120; R_Axial_DIN0207_L6.3mm_D2.5mm_P10.16mm_Horizontal
U2: L7805; TO-220-3_Vertical
U3: teensy3.2
U4: MCP2551-I-P; DIP-8_W7.62mm_Socket

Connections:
+3V3: U3.26 (3.3V)
+5V: C2.1, J2.2, J3.2, J4.2, J5.2, J6.1, J6.2, J6.3, J6.4, J6.5, J6.6, J6.7, J6.8, J7.2, U2.3 (OUT), U3.28 (Vin), U4.3 (VDD)
+BATT: C1.1, J1.1, U2.1 (IN)
/canH: J10.2, J11.2, R19.1, U4.7 (CANH)
/canL: J10.1, J11.1, R19.2, U4.6 (CANL)
/canrx: U3.6 (D4/CANRX/PWM), U4.4 (RXD)
/cantx: U3.5 (D3/CANTX/PWM), U4.1 (TXD)
GND: C1.2, C2.2, J1.2, J2.1, J3.1, J4.1, J5.1, J7.1, J8.1, J8.2, J8.3, J8.4, J8.5, J8.6, J8.7, J8.8, R17.1, U2.2 (GND), U3.1 (GND), U3.27 (AGND), U4.2 (VSS)
unnamed: J2.3, U3.7 (D5/PWM)
unnamed: J3.3, U3.8 (D6/PWM)
unnamed: J4.3, U3.9 (D7/RX3)
unnamed: J5.3, U3.10 (D8/TX3)
unnamed: J7.3, U3.16 (D14/A0)
unnamed: J7.4, U3.17 (D15/A1)
unnamed: J7.5, U3.18 (D16/A2)
unnamed: J7.6, U3.19 (D17/A3)
unnamed: J7.7, U3.20 (D18/A4/SDA0)
unnamed: J7.8, U3.21 (D19/A5/SCL0)
unnamed: J7.9, U3.22 (D20/A6/PWM)
unnamed: J7.10, U3.23 (D21/A7/PWM)
unnamed: R17.2, U4.8 (Rs)

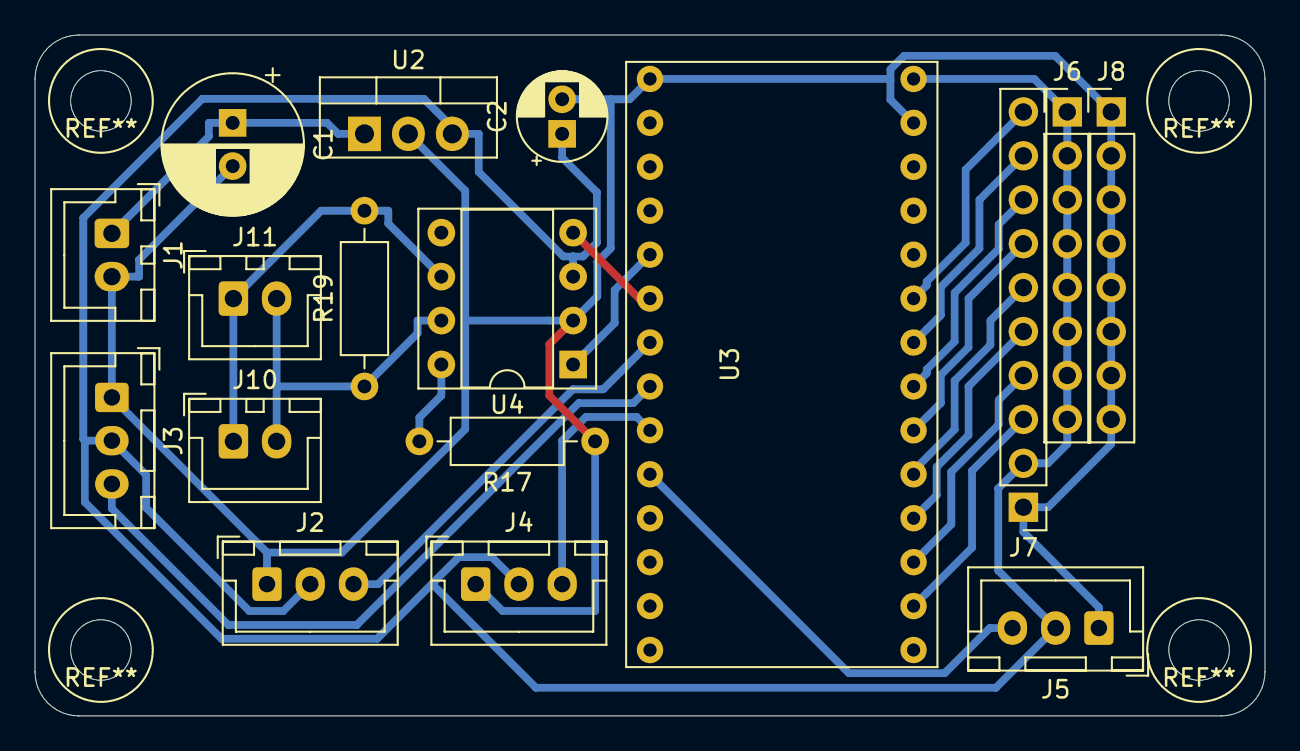
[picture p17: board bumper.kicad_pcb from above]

Board: 2 copper layers, 71.1 x 39.4 mm, 17 parts (0 on the bottom side), 20 nets.

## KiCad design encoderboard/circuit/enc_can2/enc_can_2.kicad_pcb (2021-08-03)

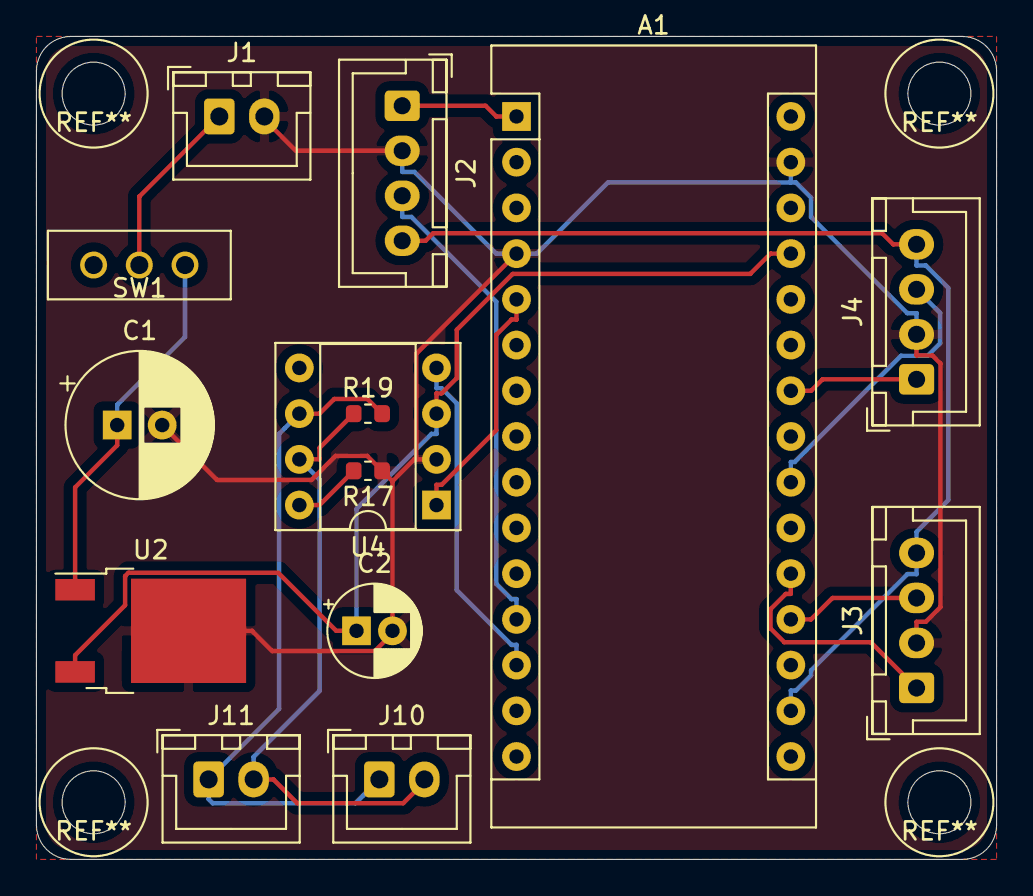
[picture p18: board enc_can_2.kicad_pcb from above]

Board: 2 copper layers, 53.3 x 45.7 mm, 14 parts (0 on the bottom side), 16 nets.

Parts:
A1: Arduino_Nano_v3.x; Arduino_Nano
C1: 220u; CP_Radial_D8.0mm_P2.50mm
C2: 100u; CP_Radial_D5.0mm_P2.00mm
J1: battery; JST_XH_B2B-XH-A_1x02_P2.50mm_Vertical
J2: ENC1; JST_XH_B4B-XH-A_1x04_P2.50mm_Vertical
J3: ENC2; JST_XH_B4B-XH-A_1x04_P2.50mm_Vertical
J4: ENC3; JST_XH_B4B-XH-A_1x04_P2.50mm_Vertical
J10: can1; JST_XH_B2B-XH-A_1x02_P2.50mm_Vertical
J11: can2; JST_XH_B2B-XH-A_1x02_P2.50mm_Vertical
R17: 10k; R_0603_1608Metric
R19: 120; R_0603_1608Metric
SW1: SW_Push_SPDT; mini_sw
U2: L7805; TO-252-2
U4: MCP2551-I-P; DIP-8_W7.62mm_Socket

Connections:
+3V3: A1.17, J2.4, J3.4, J4.4
+5V: A1.27, C2.1, U2.3, U4.3
+BATT: C1.1, SW1.3, U2.1
/ENC1_B: A1.1, J2.1
/ENC1_a: A1.12, J2.3
/ENC2_B: A1.20, J3.1
/ENC2_a: A1.19, J3.3
/ENC3_B: A1.24, J4.1
/ENC3_a: A1.22, J4.3
/canH: J10.2, J11.2, R19.1, U4.7
/canL: J10.1, J11.1, R19.2, U4.6
/canrx: A1.13, U4.4
/cantx: A1.5, U4.1
GND: A1.4, A1.29, C1.2, C2.2, J1.2, J2.2, J3.2, J4.2, R17.1, U2.2, U4.2
unnamed: J1.1, SW1.2
unnamed: R17.2, U4.8

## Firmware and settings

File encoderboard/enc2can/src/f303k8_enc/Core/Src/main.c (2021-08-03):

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
/* Includes ------------------------------------------------------------------*/
#include "main.h"

/* USER CODE BEGIN Includes */
#include "xprintf.h"
/* USER CODE END Includes */

CAN_HandleTypeDef hcan;

TIM_HandleTypeDef htim1;
TIM_HandleTypeDef htim2;
TIM_HandleTypeDef htim3;
TIM_HandleTypeDef htim16;

UART_HandleTypeDef huart2;

void SystemClock_Config(void);
static void MX_GPIO_Init(void);
static void MX_USART2_UART_Init(void);
static void MX_TIM1_Init(void);
static void MX_TIM2_Init(void);
static void MX_TIM3_Init(void);
static void MX_TIM16_Init(void);
static void MX_CAN_Init(void);
/* USER CODE BEGIN 0 */
void uart_putc(uint8_t c) {
	char buf[1];
	buf[0] = c;
	HAL_UART_Transmit(&huart2, (uint8_t*) buf, sizeof(buf), 0xFFFF);
}
TIM_Encoder_InitTypeDef sConfig1 = { 0 };
TIM_Encoder_InitTypeDef sConfig2 = { 0 };
TIM_Encoder_InitTypeDef sConfig3 = { 0 };
TIM_MasterConfigTypeDef sMasterConfig1 = { 0 };
TIM_MasterConfigTypeDef sMasterConfig2 = { 0 };
TIM_MasterConfigTypeDef sMasterConfig3 = { 0 };
int32_t rpm[3] = { 0 };
void Count2rpm() {
	rpm[0] = TIM1->CNT - 30000;
	rpm[1] = TIM2->CNT - 30000;
	rpm[2] = TIM3->CNT - 30000;
	TIM1->CNT = 30000;
	TIM2->CNT = 30000;
	TIM3->CNT = 30000;
}

//can
CAN_TxHeaderTypeDef TxHeader;
int8_t TxData[8];
uint32_t TxMailbox;
uint8_t cnt;

/* USER CODE END 0 */

/**
  * @brief  The application entry point.
  * @retval int
  */
int main(void)
{
  /* USER CODE BEGIN 1 */
	xdev_out(uart_putc);

  /* USER CODE END 1 */

  /* MCU Configuration--------------------------------------------------------*/

  /* Reset of all peripherals, Initializes the Flash interface and the Systick. */
  HAL_Init();

  /* Configure the system clock */
  SystemClock_Config();

  /* Initialize all configured peripherals */
  MX_GPIO_Init();
  MX_USART2_UART_Init();
  MX_TIM1_Init();
  MX_TIM2_Init();
  MX_TIM3_Init();
  MX_TIM16_Init();
  MX_CAN_Init();
  /* USER CODE BEGIN 2 */
	if (HAL_TIM_Encoder_Init(&htim1, &sConfig1) != HAL_OK) {
		Error_Handler();
	}
	HAL_TIM_Encoder_Start(&htim1, TIM_CHANNEL_ALL);
	TIM1->CNT = 30000;
	if (HAL_TIM_Encoder_Init(&htim2, &sConfig2) != HAL_OK) {
		Error_Handler();
	}
	HAL_TIM_Encoder_Start(&htim2, TIM_CHANNEL_ALL);
	TIM2->CNT = 30000;
	if (HAL_TIM_Encoder_Init(&htim3, &sConfig3) != HAL_OK) {
		Error_Handler();
	}
	HAL_TIM_Encoder_Start(&htim3, TIM_CHANNEL_ALL);
	TIM3->CNT = 30000;
	HAL_TIM_Base_Start_IT(&htim16);

	//can
	HAL_CAN_Start(&hcan);
	TxHeader.StdId = 0x301;
	TxHeader.RTR = CAN_RTR_DATA;
	TxHeader.IDE = CAN_ID_STD;
	TxHeader.DLC = 8;
	TxHeader.TransmitGlobalTime = DISABLE;

  /* USER CODE END 2 */

  /* Infinite loop */
  /* USER CODE BEGIN WHILE */
	while (1) {
		HAL_GPIO_TogglePin(LED_GPIO_Port, LED_Pin);
		xprintf("%d\t,%d\t,%d\t", rpm[0], rpm[1], rpm[2]);

		//can
		TxData[0] = (rpm[0]+512) & 0xFF;
//		TxData[1] = ((rpm[0]+512) >> 8) + (((rpm[1]+512) << 2) & 0xFC);
//		TxData[2] = ((rpm[1]+512) >> 6) + (((rpm[2]+512) << 4) & 0xF0);
//		TxData[3] = (rpm[2]+512) >> 4;
//		TxData[4] = 0;
//		TxData[5] = 0;
//		TxData[6] = 0;
//		TxData[7] = 10;
//
//		if (HAL_CAN_AddTxMessage(&hcan, &TxHeader, TxData, &TxMailbox)!= HAL_OK) {
//			xprintf("Can out failure!!\r\n");
//			Error_Handler();
//		} else {
//			xprintf("Can out success!!\r\n");
//		}
		HAL_Delay(10);
    /* USER CODE END WHILE */

    /* USER CODE BEGIN 3 */
	}
  /* USER CODE END 3 */
}

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


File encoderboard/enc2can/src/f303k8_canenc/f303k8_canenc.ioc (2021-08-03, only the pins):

Mcu.UserName=STM32F303K8Tx
PA0.Signal=S_TIM2_CH1_ETR
PA1.Signal=S_TIM2_CH2
PA11.Signal=CAN_RX
PA12.Signal=CAN_TX
PA13.GPIO_Label=SWDIO
PA13.Signal=SYS_JTMS-SWDIO
PA14.GPIO_Label=SWCLK
PA14.Signal=SYS_JTCK-SWCLK
PA15.GPIO_Label=VCP_RX
PA15.Signal=USART2_RX
PA2.GPIO_Label=VCP_TX
PA2.Signal=USART2_TX
PA4.Signal=S_TIM3_CH2
PA6.Signal=S_TIM3_CH1
PA8.Signal=S_TIM1_CH1
PA9.Signal=S_TIM1_CH2

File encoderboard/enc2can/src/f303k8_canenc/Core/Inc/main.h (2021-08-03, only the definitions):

#define MCO_Pin GPIO_PIN_0
#define MCO_GPIO_Port GPIOF
#define VCP_TX_Pin GPIO_PIN_2
#define VCP_TX_GPIO_Port GPIOA
#define SWDIO_Pin GPIO_PIN_13
#define SWDIO_GPIO_Port GPIOA
#define SWCLK_Pin GPIO_PIN_14
#define SWCLK_GPIO_Port GPIOA
#define VCP_RX_Pin GPIO_PIN_15
#define VCP_RX_GPIO_Port GPIOA

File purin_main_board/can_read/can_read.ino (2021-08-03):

#include <FlexCAN.h>

FlexCAN CANbus(1000000);
static CAN_message_t msg;
static CAN_message_t rxmsg;

int rpm[3] = {0};
int count[3] = {0};

void setup() {
  pinMode(13,OUTPUT);
  CANbus.begin();
  msg.id = 0x200;
  msg.len = 8;
  for (int i = 0; i < 8; i++)msg.buf[i] = 0;
}

void loop() {
  CANbus.write(msg);
  while ( CANbus.read(rxmsg) ) {
        if (rxmsg.id == 0x000) {//スイッチ_確認済
          Serial.println("0x000\tswitch");
          Serial.print("move_mode->");
          Serial.println(rxmsg.buf[0]);
          Serial.print("emergency->");
          Serial.println(rxmsg.buf[1]);
          Serial.print("reset->");
          Serial.println(rxmsg.buf[2]);
          Serial.print("start->");
          Serial.println(rxmsg.buf[3]);
          Serial.print("start->");
          Serial.println(rxmsg.buf[4]);
          Serial.println("");
        }

//        if (rxmsg.id == 0x001) {//バンパセンサ_確認済
//          Serial.println("0x001\tbumper");
//          Serial.println(rxmsg.buf[0]);
//          digitalWrite(13,rxmsg.buf[0]);
//          Serial.println("");
//        }

//        if (rxmsg.id == 0x003) {//ラインセンサ
//          Serial.println("0x003\tADC");
//          Serial.print(rxmsg.buf[0]);
//          Serial.print(",");
//          Serial.print(rxmsg.buf[1]);
//          Serial.print(",");
//          Serial.print(rxmsg.buf[2]);
//          Serial.print(",");
//          Serial.print(rxmsg.buf[3]);
//          Serial.print(",");
//          Serial.print(rxmsg.buf[4]);
//          Serial.print(",");
//          Serial.print(rxmsg.buf[5]);
//          Serial.print(",");
//          Serial.print(rxmsg.buf[6]);
//          Serial.print(",");
//          Serial.println(rxmsg.buf[7]);
//          Serial.println("");
//        }
    
//        if (rxmsg.id == 0x202) {//ハンド開閉
//          Serial.println("0x202\tm3508");
//          int16_t rotate = rxmsg.buf[0] * 256 + rxmsg.buf[1];
//          int16_t rperm = rxmsg.buf[2] * 256 + rxmsg.buf[3];
//          int16_t denryu = rxmsg.buf[4] * 256 + rxmsg.buf[5];
//          int8_t ondo = rxmsg.buf[6];
//          Serial.print("rpm->");
//          Serial.println(rperm);
//          Serial.print("rotate->");
//          Serial.println(rotate);
//          Serial.print("denryu->");
//          Serial.println(denryu);
//          Serial.print("ond->");
//          Serial.println(ondo);
//          Serial.println("");
//        }

    //    if (rxmsg.id == 0x2F1) { //core-xy位置_確認済
    //      Serial.println("0x2F1\tcore-xy_position");
    //      Serial.print("x->");
    //      Serial.println(rxmsg.buf[0] + rxmsg.buf[1] * 256);
    //      Serial.print("y->");
    //      Serial.println(rxmsg.buf[2] + rxmsg.buf[3] * 256);
    //      Serial.print("z->");
    //      Serial.println(rxmsg.buf[4] + rxmsg.buf[5] * 256);
    //      Serial.print("hand->");
    //      Serial.println(rxmsg.buf[6]);
    //      Serial.println("");
    //    }

//    if (rxmsg.id == 0x301) {//encoder速度_確認済
//      Serial.println("0x301\tencoder_speed");
//      rpm[0] = (rxmsg.buf[0] + ((rxmsg.buf[1] << 8) & 0x300)) - 512;
//      rpm[1] = (((rxmsg.buf[1] >> 2) & 0x3F) + ((rxmsg.buf[2] << 6) & 0x3F0)) - 512;
//      rpm[2] = (((rxmsg.buf[2] >> 4) & 0xF) + ((rxmsg.buf[3] << 4) & 0x3F0)) - 512;
//      Serial.print("encoder1->");
//      Serial.println((int)rpm[0]);
//      Serial.print("encoder2->");
//      Serial.println((int)rpm[1]);
//      Serial.print("encoder3->");
//      Serial.println((int)rpm[2]);
//      Serial.println("");
//    }

//    if (rxmsg.id == 0x302) {//encodercount
//      Serial.println("0x302\tencoder_count");
//      count[0] = rxmsg.buf[0] + (rxmsg.buf[1] << 8);
//      count[1] = rxmsg.buf[2] + (rxmsg.buf[3] << 8);
//      count[2] = rxmsg.buf[4] + (rxmsg.buf[5] << 8);
//      Serial.print("encoder1->");
//      Serial.println((int)count[0]);
//      Serial.print("encoder2->");
//      Serial.println((int)count[1]);
//      Serial.print("encoder3->");
//      Serial.println((int)count[2]);
//      Serial.println("");
//    }

//        if (rxmsg.id == 0x401) {//encodercount
//          Serial.println("0x401\timage_processing");
//          int ode_pos[2] = {rxmsg.buf[1] + (rxmsg.buf[2] << 8),
//                            rxmsg.buf[3] + (rxmsg.buf[4] << 8)
//                           };
//          Serial.print("object->");
//          Serial.println(rxmsg.buf[0]);
//          Serial.print("x->");
//          Serial.println(ode_pos[0]);
//          Serial.print("y->");
//          Serial.println(ode_pos[1]);
//          Serial.println("");
//        }
  }
  delay(10);
}

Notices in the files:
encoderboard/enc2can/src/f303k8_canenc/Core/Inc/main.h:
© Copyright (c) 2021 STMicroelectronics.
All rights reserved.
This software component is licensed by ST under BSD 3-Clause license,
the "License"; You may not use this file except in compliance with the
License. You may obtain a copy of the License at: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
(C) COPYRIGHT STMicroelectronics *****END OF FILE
